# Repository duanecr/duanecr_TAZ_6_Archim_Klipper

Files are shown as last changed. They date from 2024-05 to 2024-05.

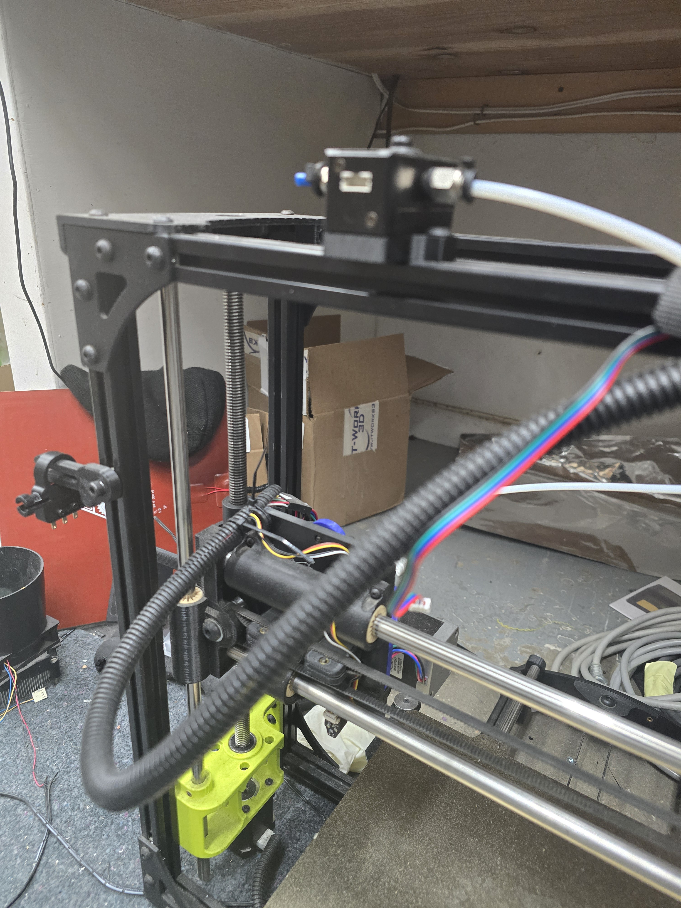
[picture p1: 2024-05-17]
TAZ6_Project/Manuals/SFS V2.0 Mount Location 2.jpg

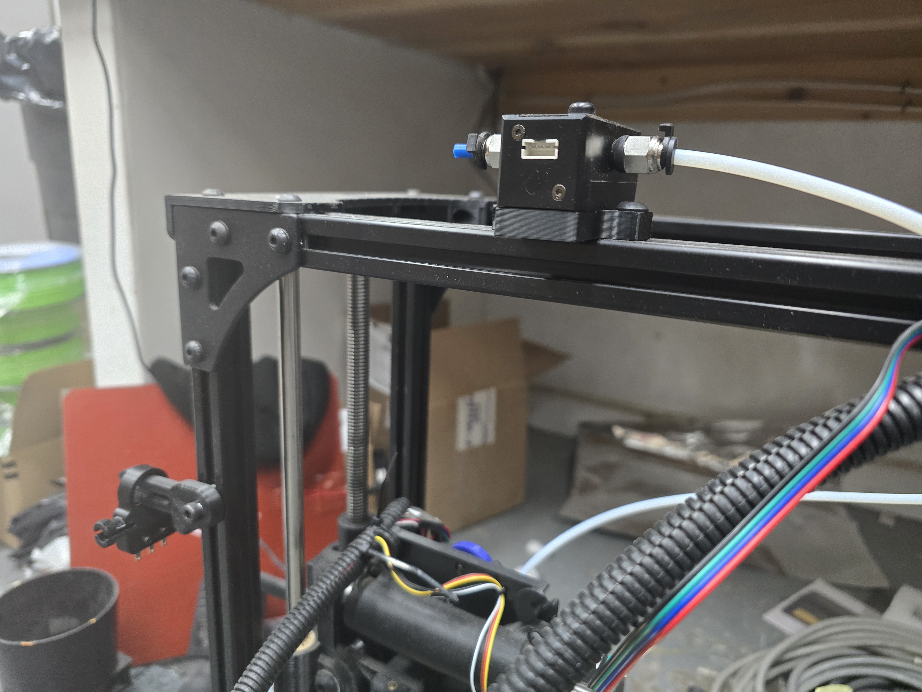
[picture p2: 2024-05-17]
TAZ6_Project/Manuals/SFS V2.0 Mount Location 1.jpg

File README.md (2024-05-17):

# duanecr_TAZ_6_Archim_Klipper
Configuration files for Lulzbot TAZ 6 using an Archim 2 board with a BTT PAD 7 for Klipper

Klipper Links

https://www.klipper3d.org/

https://github.com/Klipper3d/klipper

https://github.com/Klipper3d/klipper/tree/master/docs

Mainsail documentation
https://docs.mainsail.xyz/

**Initial Setup and Configuration**
• Install Klipper on a device if needed
○ Installation - Klipper documentation (klipper3d.org)
https://www.klipper3d.org/Installation.html
• Install Moonraker
	○ Installation - Moonraker
	https://moonraker.readthedocs.io/en/latest/installation/
• Install Klipperscreen for touchscreens
	○ Installation - KlipperScreen
	https://klipperscreen.readthedocs.io/en/latest/Installation/#auto-install
• Install Lulzbot version of Cura
	○ https://www.lulzbot.com/cura
• Verify printer bed is clean and empty
• Turn on printer
• Turn on device running Klipper
• Verify amount of filament on spool
• Verify thickness of filament for imperfections
• Connect web browser to http://taz.local and verify connectivity
• Open Cura and run through install steps for local printer
• Install Moonraker plugin for Cura
• Connect to Klipper
• Set the theme settings
	○ Lulzbot Lime Green
		§ rgb(194, 215, 53)
		○ Mainsail Quicktips | Themes
	https://youtu.be/kbSfLQtl4tA?si=HL7WomTxeTPDtKlo
	• Check E-Steps by running ??? command.
	• Use Orca calibration to check all of the settings
		○ Calibration · SoftFever/OrcaSlicer Wiki (github.com)
  		https://github.com/SoftFever/OrcaSlicer/wiki/Calibration

**Cura Print Settings**
Build plate adhesion type, determine whether to print on raft, skirt, or brim
Generate support or tree support
Infill density
Uncheck "keep heating" for build plate in Material section
Change "Z Seam Alignment" to shortest or random for round prints
 
**Initial Calibration Sites**
Teaching Tech 3D Printer Calibration (teachingtechyt.github.io)
https://teachingtechyt.github.io/calibration.html
Welcome! | Ellis’ Print Tuning Guide (ellis3dp.com)
https://ellis3dp.com/Print-Tuning-Guide/
 
New Printer Setup
Complete beginner's guide to 3D printing - Assembly, tour, slicing, levelling and first prints
https://youtu.be/T-Z3GmM20JM
 
Verify Extruder E-Steps
Run 100mm of filament through extruder to verify it is correct.  Adjust as needed.
[Teaching Tech 3D Printer Calibration (teachingtechyt.github.io)](https://teachingtechyt.github.io/calibration.html#esteps)

Set PID Autotune
[G-Codes - Klipper documentation (klipper3d.org)](https://www.klipper3d.org/G-Codes.html#pid_calibrate_1)
https://www.klipper3d.org/Config_checks.html?h=pid_calibrate#calibrate-pid-settings
PID_CALIBRATE HEATER=<config_name> TARGET=<temperature> [WRITE_FILE=1]
PID_CALIBRATE HEATER=heater_bed TARGET=60
PID_CALIBRATE HEATER=extruder TARGET=205

SAVE_CONFIG

Set Z Offset
Check Z-Offset
[Probe calibration - Klipper documentation (klipper3d.org)](https://www.klipper3d.org/Probe_Calibrate.html?h=z+offset#calibrating-probe-z-offset)
PROBE_CALIBRATE
SAVE_CONFIG
PROBE_ACCURACY

Resonance Compensation
https://www.klipper3d.org/Resonance_Compensation.html

Pressure Advance
https://www.klipper3d.org/Pressure_Advance.html

Bed Mesh Calibration
https://www.klipper3d.org/G-Codes.html#bed_mesh_calibrate
 
Calibration Source Information
https://teachingtechyt.github.io/calibration.html
Retraction calibration code site - http://prahjister.duckdns.org

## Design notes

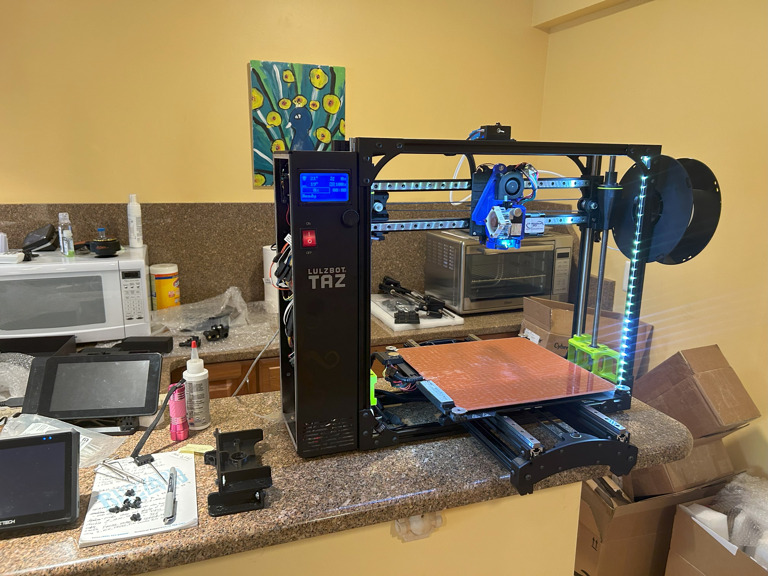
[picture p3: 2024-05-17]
TAZ6_Project/Pictures/20240410_190605491_iOS.jpg

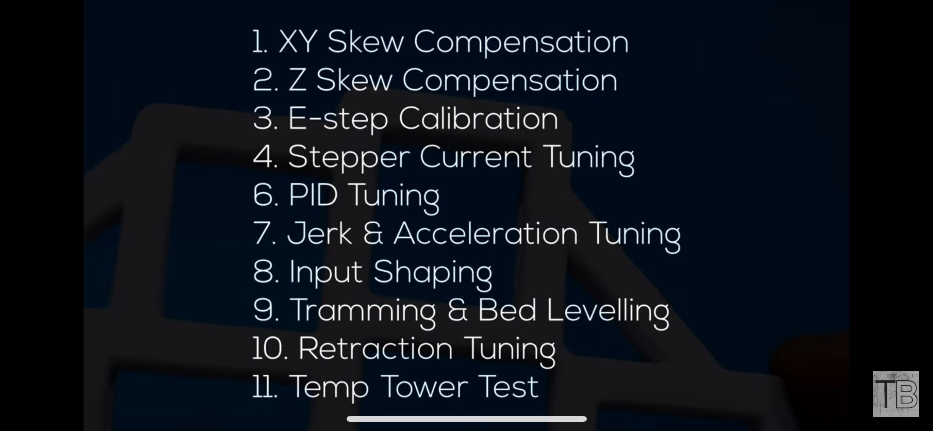
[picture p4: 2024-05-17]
TAZ6_Project/Pictures/20240403_203024000_iOS.png

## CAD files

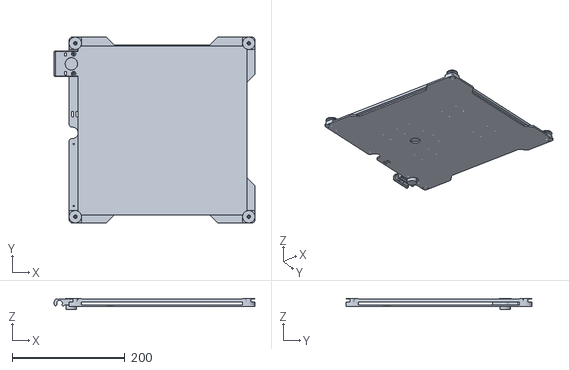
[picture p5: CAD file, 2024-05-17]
TAZ6_Project/Lulzbot TAZ 6 Build Plate.stl
356.9 x 330.0 x 20.2

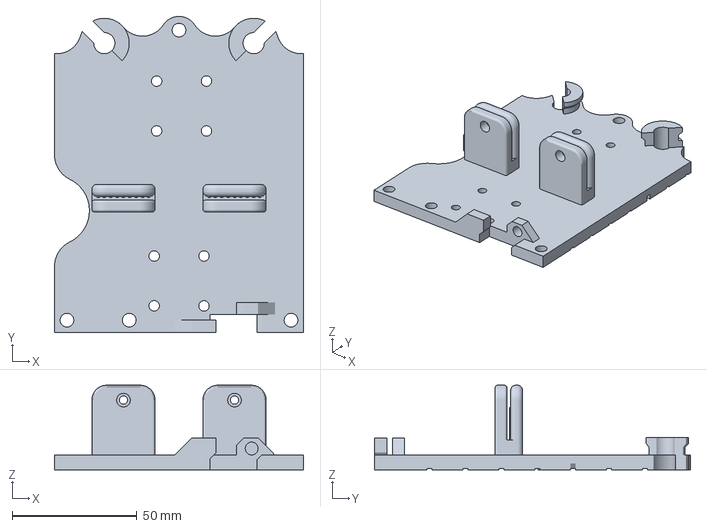
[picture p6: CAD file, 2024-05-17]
TAZ6_Project/Manuals/3D Models/TAZ 6 X Carriage Biqu MicroProbe Mount_LinearRail.3mf
100.0 x 127.0 x 34.0 mm

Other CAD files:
TAZ6_Project/Lulzbot TAZ 6 Build Plate.f3d

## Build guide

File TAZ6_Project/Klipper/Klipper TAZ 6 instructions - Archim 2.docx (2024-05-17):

Klipper/Touch Screen instructions for TAZ 6

These steps will get you setup with basic Klipper and MainSail to operate your TAZ 3D Printer. We would recommend familiarizing yourself with Klipper Language a bit via web search/YouTube videos. This will help your installation

First thing we recommend is to remove the SD card from the Pad7 and back-up all the files onto your computer somewhere just in case anything happens to it.

First things we will be doing is installing the new X Carriage. We have provided an ABS X Carriage that you will install onto your carriage mounts that has a built in spot for the Biqu MicroTouch ABL sensor. There are 2 screws/serts that you will use to install the probe onto the X carriage before installing it onto your printer. Remove your existing X carriage. Once the probe is installed correctly, install the Entire x carriage onto your printer. You can run a new belt at this point if you have one. You will re-use your current lower toolhead mount on the bottom of the X carriage. There are zip tie locations built into the X Carriage to route your wiring up the backside of the carriage for the MicroProbe.

You will need to run the wiring from the MicroProbe to the back of the machine where the wiring goes into the control box. You can run it in the same wiring that the toolhead wiring goes through. You will need to remove the small interconnect cover that houses the connections from the external wiring to the internal wiring (six screws). We have supplied a lengthened wiring harness that will connect the MicroProbe to the Rambo. See the Diagram below to see where the connectors will plug in. You will need to remove the wiring for the Z min endstop. The White and Black wires will plug into the Z-Min end-stop location, white wire to the left side. The Red/Brown will plug into the Serial connector location to the far right just to the left of the single 5 amp fuse. The brown wire will go into the top right pin. Yellow will go into pin 20 in the SPIO connector

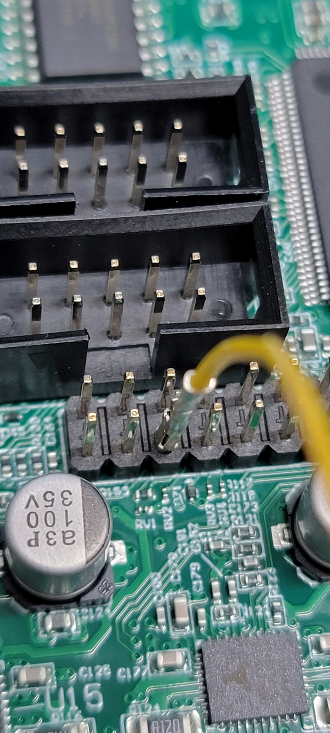
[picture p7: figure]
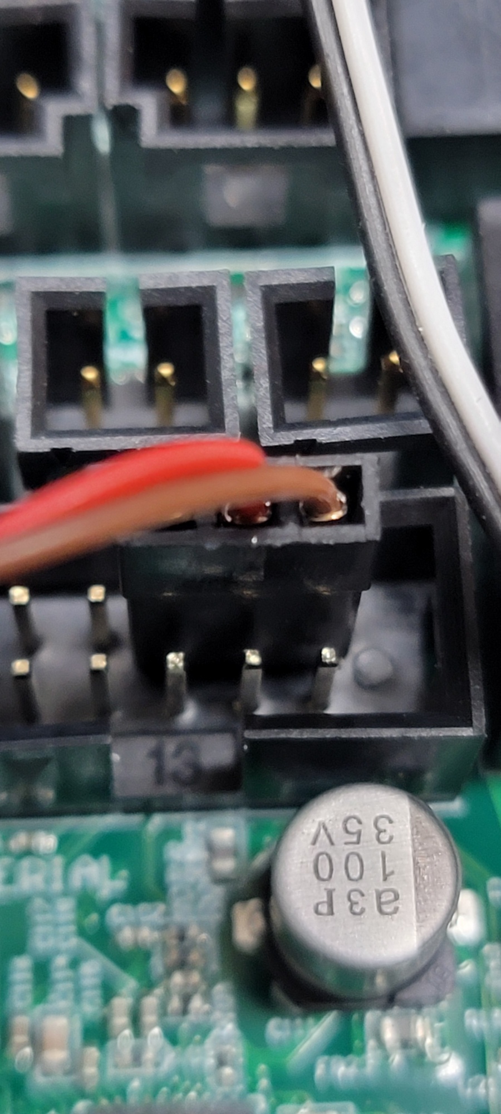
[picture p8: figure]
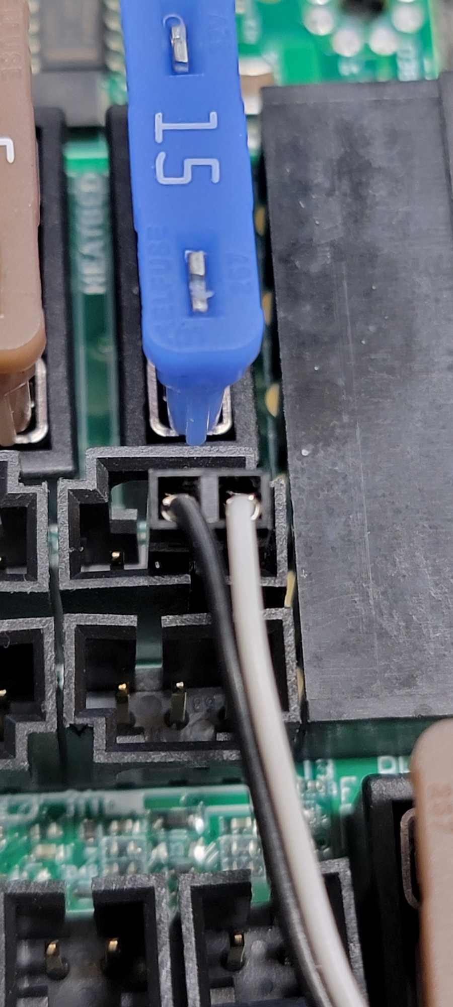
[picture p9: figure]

Button up all the wiring in the control box, and reinstall the interconnect cover. You can either add a new small section of wiring loom, or install it in to the current loom (it’s a bit tight already). If you add a new loom for the probe, just zip tie it to the existing toolhead harness all the way down to your toolhead. Re-install your toolhead and toolhead connector.

You will need to remove your BTT Pad 7 from the box and find a suitable location for it next to your printer. It will require a power box to be plugged in so make sure you have enough plug-ins available at your printer location. When turning it on, you will want to go ahead and set your Wi-Fi up with your SSID and password. Once you set it setup. Go ahead and restart the touchpad, and bring up your Wi-Fi menu once again and it should show you the IP Address that has been designated.

You will need to download a program called Putty so that you can SSH into your Pad7. If you search for Putty Download, you should see it come up. Get it setup on your computer you will be using to talk to your Pad7. Open the Putty program and you will see a window with Host Name. Enter in btt-pad7 and the SSH button below should be checked. Click Open at the bottom of the window. A new screen will open up and ask you for a user and password. Both user and password are biqu/biqu. From there you will be logged into the pad7. Complete the following steps to build and flash the Klipper Firmware to your printer Main Board (Rambo). Be sure you have a USB cable attached from y our Pad7 to the TAZ printer. It will need to be connected from here on out.

Type cd ~/klipper/

Type make menuconfig

Configure your settings according to the micro controller you are using.

Stock Rambo board (Taz6, Mini1, Mini2)

AVR atmega2560

Archim2 board (Taz6)

SAM3x8e

Type make

Plug in the printer via USB to pi and power it on.

Type ls /dev/serial/by-id/*

You printer should appear and look something like this. This is a unique ID and you'll need it later for the config file as well.

/dev/serial/by-id/usb-1a86_USB2.0-Serial-if00-port0

Now it's time to flash your board. Replace the ID with the one you got in the previous step.

Type sudo service klipper stop

Type make flash FLASH_DEVICE=/dev/serial/by-id/usb-1a86_USB2.0-Serial-if00-port0(this ID is just used for example, use the one provided in earlier steps)

Type sudo service klipper start

Reboot everything type sudo reboot

You will need to use the ID that you got from these steps in your printer.cfg file that we provide so it can talk to your printer. You will copy and paste that into the printer.cfg file a bit later on. You can go ahead and close out of your Putty Config window.

You can now use the IP address that your Pad7 got earlier on in the Wi-Fi steps. Type it into your browser with your Pad7 turned on. You will see an error message for now, but please disregard this for the time being. Once you are logged into the PAD7 from your browser you will see a set of icons on the left side of your screen. Click the machine icon, and this will open up a window that will show your configuration files associated with the PAD7 and klipper. You will need to upload the files for this part of the install; printer.cfg, that has been provided to you. Once the printer.cfg uploaded, open the printer.cfg file and up top you will need to paste your /dev/serial/by-id/* up top in the printer.cfg file so it can communicate with the board. You will need to go back to your Dashboard and then restart your firmware so it can communicate with the new build. The error that was on your screen should now be gone, and you should have a screen that shows homing, temperatures, etc.

The printer.cfg file is where the toolhead/stepper motor/printer info is stored. We have supplied you with files that you will need to rename to printer.cfg for them to work properly. You will need to be sure in the printer.cfg file, your toolhead does NOT have hash tags in front of each line. There should be a section for the stock toolhead, and a section for a Titan Aero toolhead. There you can set your filament diameter as well.

At this point make sure you X Axis is level across the bed meaning that you could run your nozzle across manually and it would be the same from the left side of the bed to the right. Turn your threaded rods until you can run it across and have it be the same on both sides. You can then click the Home button for each axis to ensure everything is working and moving as it should. X axis should home to the left side, the Y axis should home to the Back, and Z should go to the middle of the bed, and probe that location for Z. When you are homing each axis, be close to your printer on/off switch in case anything goes wrong.

Heat your bed up to at least 60C or whatever filament temp you are normally printing with. From your browser or the Pad7, you should be able to go into your height map menu or the config menu on the pad7 and go into bed mesh, and start the calibration. This will show you what your bed looks like and create a map for it to get the best first layer. In some cases you may need to shim your bed corners depending on what your first layer looks like if it can either compensate for it, or not. That will all depend on your bed. Again, be sure your X axis is level with the bed. It will give you the best possible starting point.

If you have specific Estep numbers saved from before, this is when you will change them. You can find a Estep to rotation distance convertor by searching online. Once you get that number you can replace it with the current rotation distance. You can check by telling the printer to extrude 100mm of filament and physically marking your filament at 100mm to ensure it send 100mm through it from the top at printing temperature.

We have the printer.cfg file setup to print a purge line at the front of the bed before it makes it over to your print. If you want this turned off, you can find the purge line in the cfg file, and put a hash in front of it to comment it out and not do the purge line.

How to install the 1.75mm Filament Runout/Motion Sensor

You will start by mounting your filament runout sensor in whichever configuration you want to run your filament with. We have provided a bracket for both top side configuration and a Top only configuration. See pics below for how we mounted our 1.75mm runout sensor. If you want to create your own bracket, reach out to us we can provide you with a STEP file to create your own based on your needs.

We have pinned your filament runout sensor so all you have to do is put the wires to their correct locations. Looking at the 24 pin SPIO connector, the Red will go into pin 24, black on pin 23 Blue on Pin 16 and green will do to Pin 15. SEE PICS FOR LOCATIONS.

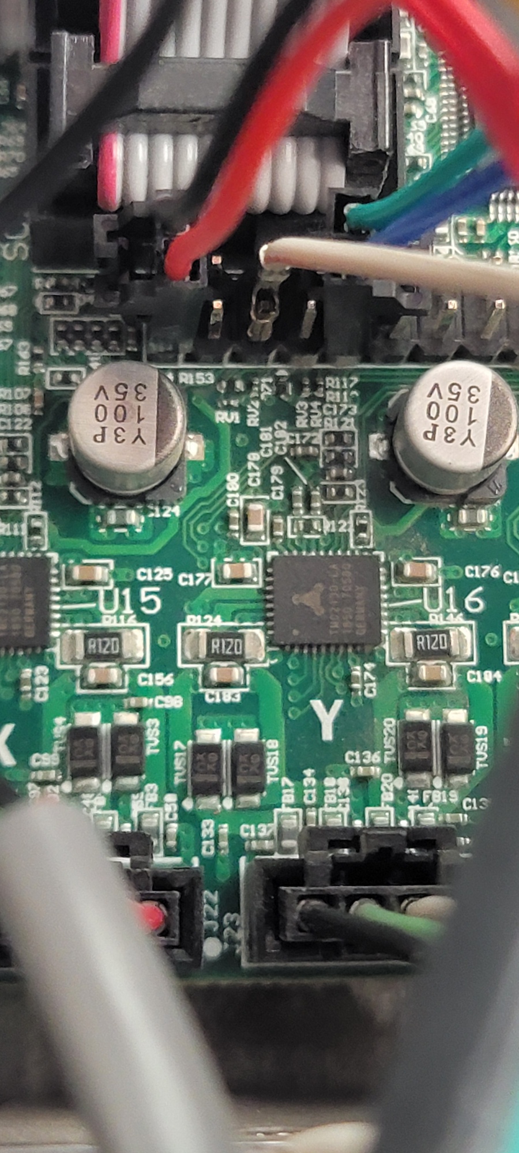
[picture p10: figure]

Keep in mind, the filament run-out/motion sensor will only work with 1.75mm filament. Now would be a great time to upgrade to a 1.75mm toolhead if you don’t already have one. We offer a wide range of 1.75mm toolheads. Toolhead that flow more and can keep up with higher speeds can be beneficial here. CHT nozzles as well as things like REVO HF can help out with that as well.

How to install the 2.85mm Filament Runout Switch

The 2.85/3mm sensor will install into some of the same pins as the 1.75mm, so if you are using the 2.85mm just swap the connectors for the pins shown in the photos below. You will be using the SPIO connector for this and the red will go into the 2nd pin to the right from the yellow wire from the MicroProbe, and the black will go into the Serial Connector lower left pin. Bottom left pin which is a ground. The red wire in this setup goes in the same location as the blue wire in the 1.75mm sensor. See pic above for location image.

HOW TO SETUP AND USE THE ADXL345 FOR INPUT SHAPER

We have already added the file necessary to use the ADXL345 provided with the PAD7. We have also added the necessary config tags into the printer.cfg file and adxl.cfg file that is necessary to work.

Start with the units power off, plug the adxl345 harness into the sensor itself, and then into the Pad7. To run input shaper on the y axis you will need to remove your wiper pad from the Y axis. You can use one of the screws to mount your adxl sensor to the bed plate. Make sure your wiring can move to the and have it not overextend or get caught anywhere. You will need to go into your printer.cfg file and remove the # from [include adxl.cfg]. Go into your console and run the following command: accelerometer_query. You should get a reading if working as it should. Home all axis, then you will type in shaper_calibrate axis=y. It will run a series of resonance tests. Once it’s finished up, it will show you the results, and ask you to save config. Go ahead and save, then restart Klipper and let it come back up to the dashboard. Go back into your printer.cfg file, and then scroll down to the very bottom. You should see those results posted there. Now you will be the same for your X axis. Attach the adxl to your toolhead somewhere, we mounted ours to one screw on the fan. Run the test again, and save like before. Save config and go back into your printer.cfg file and scroll to the bottom again and see if it saved those settings. If so you are done with input shaping. Keep in mind you will be required to do any tuning to your printer. We will not provide profiles for anything. Input shaping can only help so much so be sure to perform any calibration prints as necessary to get the best possible prints.

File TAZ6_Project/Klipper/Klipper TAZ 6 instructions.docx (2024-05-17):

Klipper/Touch Screen instructions for TAZ 6

These steps will get you setup with basic Klipper and MainSail to operate your TAZ 3D Printer. We would recommend familiarizing yourself with Klipper Language a bit via web search/YouTube videos. This will help your installation

First thing we recommend is to remove the SD card from the Pad7 and back-up all the files onto your computer somewhere just in case anything happens to it.

First thing we will be doing is installing the new X Carriage. If you have a linear rail conversion and we sent you the X carriage for a stock setup, please let us know we can get you the correct X Carriage.

There are 2 screws/serts that you will use to install the probe onto the X carriage before installing it onto your printer. Remove your existing X carriage. Once the probe is installed correctly, install the Entire x carriage onto your printer. You can run a new belt at this point if you have one. You will re-use your current lower toolhead mount on the bottom of the X carriage. There are zip tie locations built into the X Carriage to route your wiring up the backside of the carriage for the MicroProbe.

You will need to run the wiring from the MicroProbe to the back of the machine where the wiring goes into the control box. You can run it in the same wiring that the toolhead wiring goes through. You will need to remove the small interconnect cover that houses the connections from the external wiring to the internal wiring (six screws). We have supplied a wiring harness that will connect the MicroProbe to the Rambo/Archim. See the Diagram below to see where the connectors will plug in. You will need to remove the wiring for the Z min endstop. The White and Black wires will plug into the Z-Min endstop location. The Red/Brown will plug into the Motor EXT1 MX3 location to the far right. Red pin will go in the #1 location and brown right next to it. The Yellow will plug into the MX1 position #3 which is the bottom of EXT1 in the very middle.

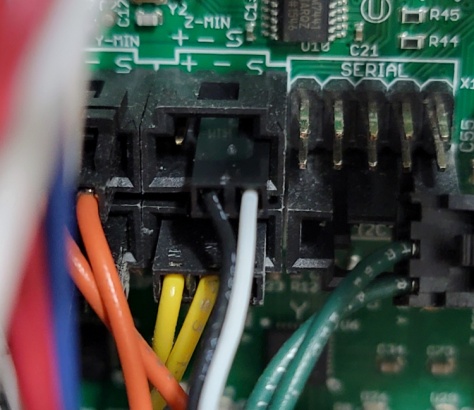
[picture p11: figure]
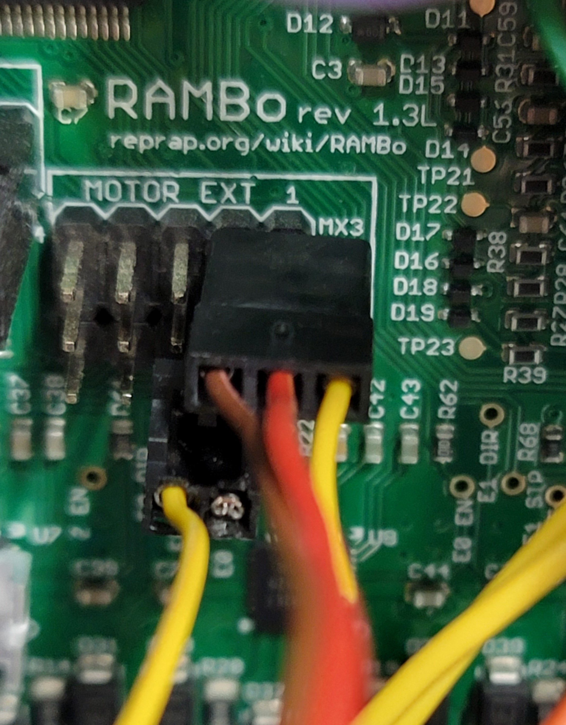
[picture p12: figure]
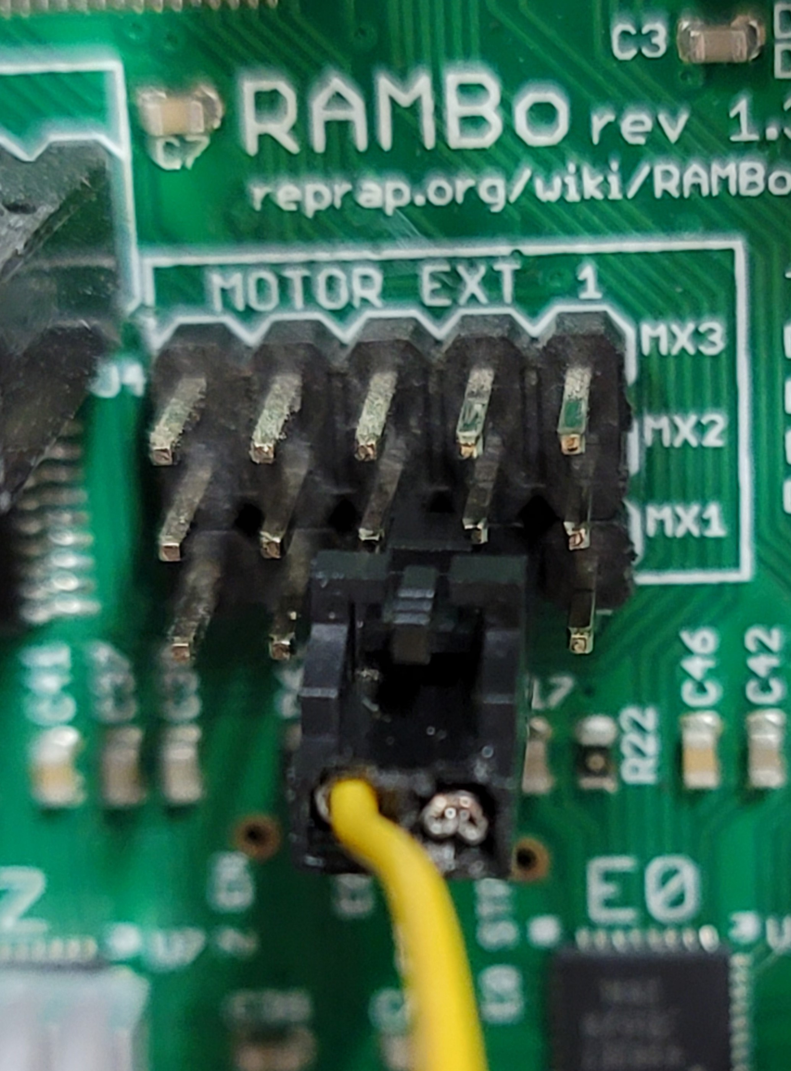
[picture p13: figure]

Button up all the wiring in the control box, and reinstall the interconnect cover. You can either add a new small section of wiring loom, or install it in to the current loom (it’s a bit tight already). If you add a new loom for the probe, just zip tie it to the existing toolhead harness all the way down to your toolhead. Re-install your toolhead and toolhead connector.

Next, you will need to remove your BTT Pad 7 from the box and find a suitable location for it next to your printer. It will require a power box to be plugged in so make sure you have enough plug-ins available at your printer location. When turning it on, you will want to go ahead and set your Wi-Fi up with your SSID and password. Once you set it setup. Go ahead and restart the touchpad, and bring up your Wi-Fi menu once again and it should show you the IP Address that has been designated.

You will need to download a program called Putty so that you can SSH into your Pad7. If you search for Putty Download, you should see it come up. Get it setup on your computer you will be using to talk to your Pad7. Open the Putty program and you will see a window with Host Name. Enter in btt-pad7 and the SSH button below should be checked. Click Open at the bottom of the window. A new screen will open up and ask you for a user and password. Both user and password are biqu/biqu. From there you will be logged into the pad7. Complete the following steps to build and flash the Klipper Firmware to your printer Main Board (Rambo). Be sure you have a USB cable attached from y our Pad7 to the TAZ printer. It will need to be connected from here on out.

Type cd ~/klipper/

Type make menuconfig

Configure your settings according to the micro controller you are using.

Stock Rambo board (Taz 5, 6)

AVR atmega2560

or

Archim2 board (Taz6)

SAM3x8e

Type make

Plug in the printer via USB to pi and power it on.

Type ls /dev/serial/by-id/*

You printer should appear and look something like this. This is a unique ID and you'll need it later for the config file as well.

/dev/serial/by-id/usb-1a86_USB2.0-Serial-if00-port0

Now it's time to flash your board. Replace the ID with the one you got in the previous step.

Type sudo service klipper stop

Type make flash FLASH_DEVICE=/dev/serial/by-id/usb-1a86_USB2.0-Serial-if00-port0(this ID is just used for example, use the one provided in earlier steps)

Type sudo service klipper start

Reboot everything type sudo reboot

You will need to use the ID that you got from these steps in your printer.cfg file that we provide so it can talk to your printer. You will copy and paste that into the printer.cfg file a bit later on. You can go ahead and close out of your Putty Config window.

You can now use the IP address that your Pad7 got earlier on in the Wi-Fi steps. Type it into your browser with your Pad7 turned on. You will see an error message for now, but please disregard this for the time being. Once you are logged into the PAD7 from your browser you will see a set of icons on the left side of your screen. Click the machine icon, and this will open up a window that will show your configuration files associated with the PAD7 and klipper. You will need to upload the files for this part of the install; printer.cfg, that has been provided to you. Once the printer.cfg uploaded, open the printer.cfg file and up top you will need to paste your /dev/serial/by-id/* up top in the printer.cfg file so it can communicate with the board. You will need to go back to your Dashboard and then restart your firmware so it can communicate with the new build. The error that was on your screen should now be gone, and you should have a screen that shows homing, temperatures, etc.

The printer.cfg file is where the toolhead/stepper motor/printer info is stored. We have supplied you with files that you will need to rename to printer.cfg for them to work properly. You will need to be sure in the printer.cfg file, your toolhead does NOT have hash tags in front of each line. There should be a section for the stock toolhead, and a section for a Titan Aero toolhead. There you can set your filament diameter as well.

For setting your toolhead esteps you will be changing the Rotation distance on the [extruder] portion of the cfg file. Again, you will also see there is a setup for either the stock toolhead or a Titan Aero toolhead. If you are going to use the Titan Aero you will need put a hash in from of the stock extruder settings or vice versa, and remove the hash from the extruder you wish to use.

At this point make sure you X Axis is level across the bed meaning that you could run your nozzle across manually and it would be the same from the left side of the bed to the right. Turn your threaded rods until you can run it across and have it be the same on both sides. You can then click the Home button for each axis to ensure everything is working and moving as it should. X axis should home to the left side, the Y axis should home to the Back, and Z should go to the middle of the bed, and probe that location for Z. When you are homing each axis, be close to your printer on/off switch in case anything goes wrong.

Heat your bed up to at least 60C or whatever filament temp you are normally printing with. From your browser or the Pad7, you should be able to go into your height map menu or the config menu on the pad7 and go into bed mesh, and start the calibration. This will show you what your bed looks like and create a map for it to get the best first layer. In some cases you may need to shim your bed corners depending on what your first layer looks like if it can either compensate for it, or not. That will all depend on your bed. Again, be sure your X axis is level with the bed. It will give you the best possible starting point.

If you have specific Estep numbers saved from before, this is when you will change them. You can find a Estep to rotation distance convertor by searching online. Once you get that number you can replace it with the current rotation distance. You can check by telling the printer to extrude 100mm of filament and physically marking your filament at 100mm to ensure it send 100mm through it from the top at printing temperature.

We have the printer.cfg file setup to print a purge line at the front of the bed before it makes it over to your print. If you want this turned off, you can find the purge line in the cfg file, and put a hash in front of it to comment it out and not do the purge line.

How to install the 1.75mm Filament Runout/Motion Sensor

You will start by mounting your filament runout sensor in whichever configuration you want to run your filament with. We have provided a bracket for both top side configuration and a Top only configuration. See pics below for how we mounted our 1.75mm runout sensor. If you want to create your own bracket, reach out to us we can provide you with a STEP file to create your own based on your needs.

We have pinned your filament runout sensor so all you have to do is put the connectors to their correct locations. Red will go into pin 1, black on pin 2 Blue on Pin 7 of the X40 Connector. Green will do to Pin 5 on the X34 connector. SEE PICS FOR LOCATIONS.

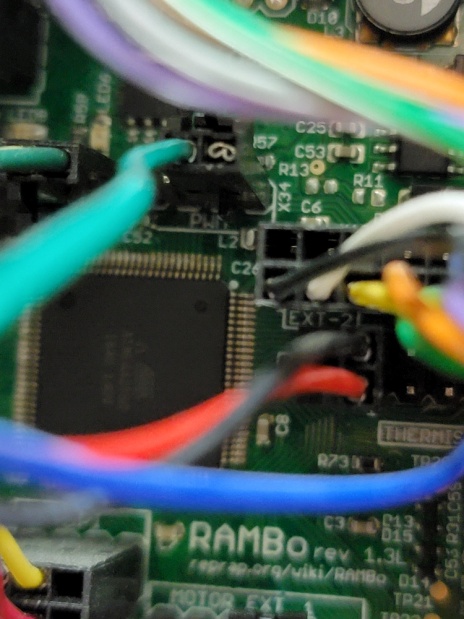
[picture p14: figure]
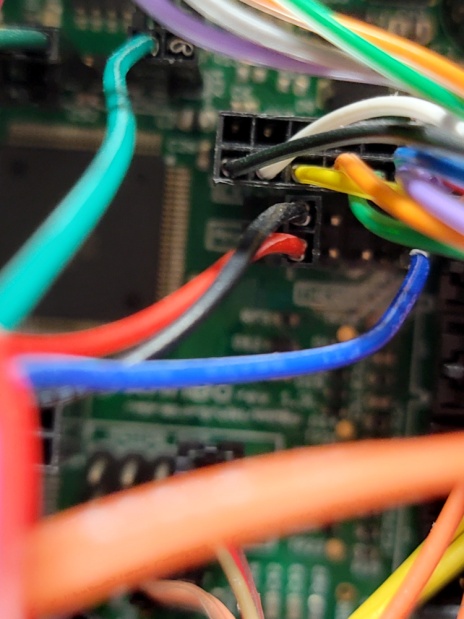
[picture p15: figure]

We have showed the connections with the Rambo 1.3L Main Board. These same instructions will work for the 1.4 as well, but one connector location is a bit different. You will need to locate the X34 and X 40 connectors. The X34 set is a 6 pin in line configuration just above the largest main chip on the board. The X 40 is over to the right side of the largest chip on the board.

Keep in mind, the filament run-out/motion sensor will only work with 1.75mm filament. Now would be a great time to upgrade to a 1.75mm toolhead if you don’t already have one. We offer a wide range of 1.75mm toolheads. Toolhead that flow more and can keep up with higher speeds can be beneficial here. CHT nozzles as well as things like REVO HF can help out with that as well.

How to install the 2.85mm Filament Runout Switch

The 2.85/3mm sensor will install into some of the same pins as the 1.75mm, so if you are using the 2.85mm just swap the connectors for the pins shown in the photos below. You will be using Pin 2 for the black wire, and pin 7 for the red wire of the X40 Connector.

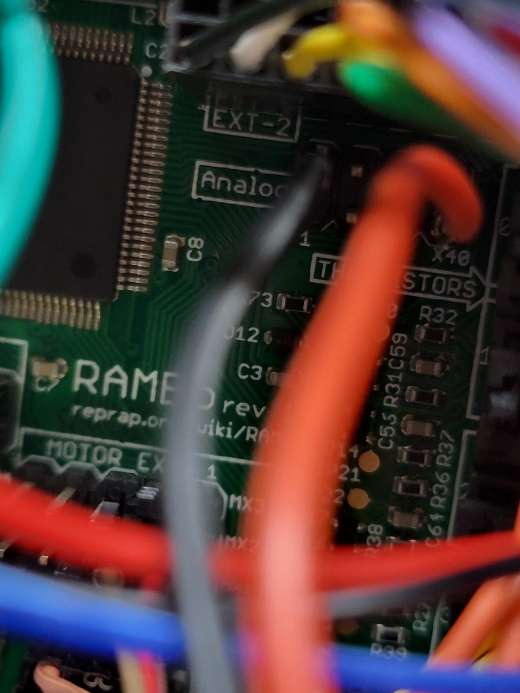
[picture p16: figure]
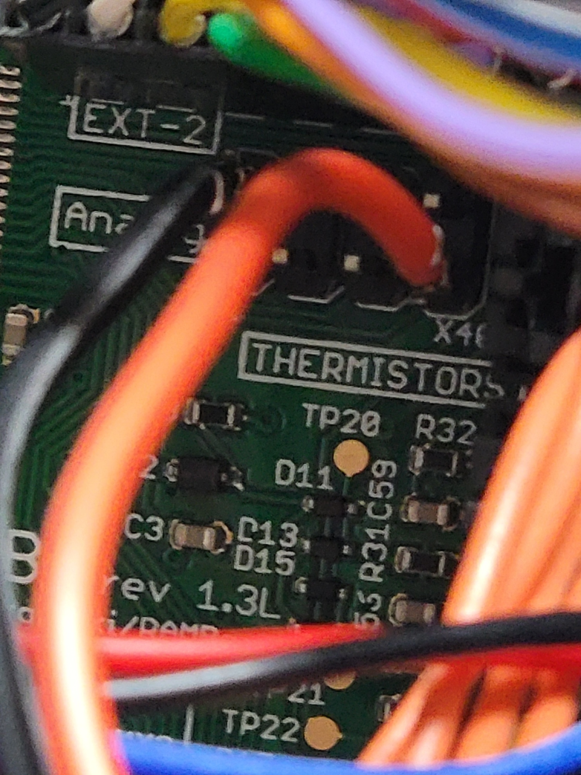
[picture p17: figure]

HOW TO SETUP AND USE THE ADXL345 FOR INPUT SHAPER

We have already added the file necessary to use the ADXL345 provided with the PAD7. We have also added the necessary config tags into the printer.cfg file and adxl.cfg file that is necessary to work.

Start with the units power off, plug the adxl345 harness into the sensor itself, and then into the Pad7. To run input shaper on the y axis you will need to remove your wiper pad from the Y axis. You can use one of the screws to mount your adxl sensor to the bed plate. Make sure your wiring can move to the and have it not overextend or get caught anywhere. You will need to go into your printer.cfg file and remove the # from [include adxl.cfg]. Go into your console and run the following command: accelerometer_query. You should get a reading if working as it should. Home all axis, then you will type in shaper_calibrate axis=y. It will run a series of resonance tests. Once it’s finished up, it will show you the results, and ask you to save config. Go ahead and save, then restart Klipper and let it come back up to the dashboard. Go back into your printer.cfg file, and then scroll down to the very bottom. You should see those results posted there. Now you will be the same for your X axis. Attach the adxl to your toolhead somewhere, we mounted ours to one screw on the fan. Run the test again, and save like before. Save config and go back into your printer.cfg file and scroll to the bottom again and see if it saved those settings. If so you are done with input shaping. Keep in mind you will be required to do any tuning to your printer. We will not provide profiles for anything. Input shaping can only help so much so be sure to perform any calibration prints as necessary to get the best possible prints.

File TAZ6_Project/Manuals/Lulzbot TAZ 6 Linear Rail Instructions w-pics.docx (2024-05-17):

Lulzbot TAZ 5/6 Y Axis Linear Rail
Conversion Instructions

IF DURING ANY POINT OF INSTALLATION YOU HAVE QUESTIONS, CALL OR EMAIL US BEFORE MOVING TO NEXT STEP.

First. Unplug the printer. Then, remove the 4 thumbscrews that hold your bed down to the printer. Then unplug the Y axis motor, Bed heater, thermistor and switch wiring. Remove the entire bed assembly from the printer and place in an easy to work in space.

Remove the 4 bed washers, screws and spacers from the bed assembly. Remove the build plate and set it aside somewhere safe. Turn the bed assembly upside down so you can see the bushing holders. Remove the 4 M3x8 button head screws that hold down each bushing holder and save the screws and washers as you will use these screws to mount the drill jig to the aluminum plate (shown in the images). Remove the 4 M3x8 button head screws and washers that hold down the Belt Mount. Remove the 4 M3x8 button head screws and washers that hold the Y End Idler on the front Y End Plate. Remove the 4 M3x8 button head screws and washers that hold on the Y End Motor Mount to the rear Y End Plate.

Mount the supplied 3D printed drill jigs to the aluminum bed plate with the M3x8 button head screws and washers you removed in the previous step.

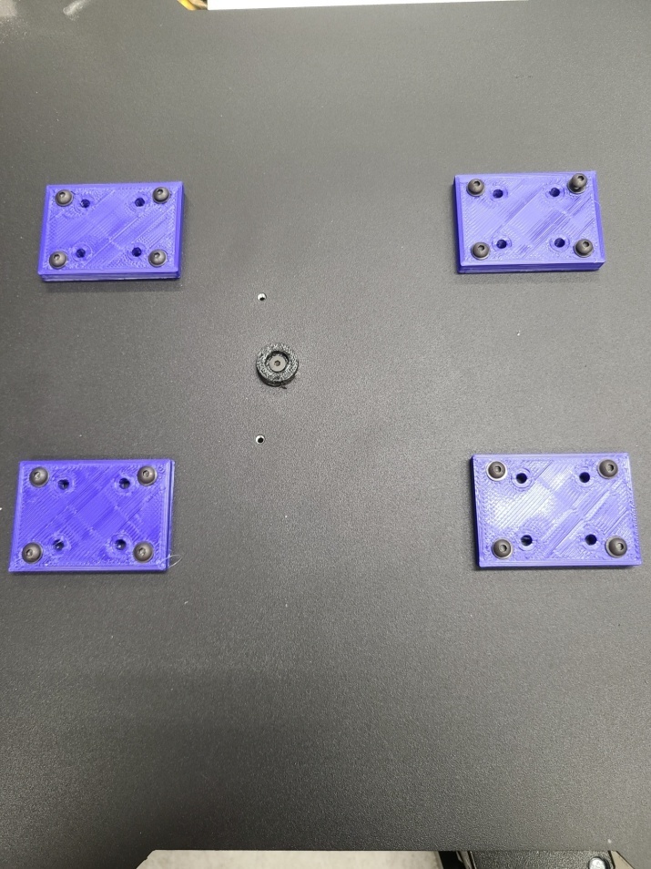
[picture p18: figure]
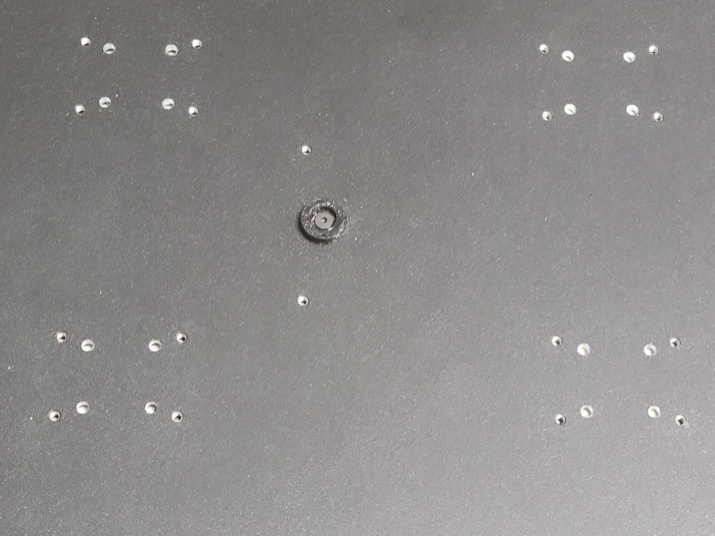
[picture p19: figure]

Place the aluminum bed plate on something flat like a piece of plywood. This will ensure you do not bend the aluminum plate. Drill each hole out with the supplied 9/16” drill bit. Now remove the drill jigs and deburr each hole drilled with a larger drill bit by hand spinning the bit just over each hole You want the hole free of anything sticking off of it so the linear rail carriage mounts flush.

Loosen the set screws that hold the smooth rods onto the 3d printer corners and remove them from the assembly. You can put the bushing holders back onto the rods and set them aside for storage. Remove the M5x10 button head screws and washers from the Y end plates from the bed assembly being sure to keep all hardware. Remove the M5x10 button head screws and washers holding the 3d printer corners/bed feet again keeping the hardware as it will go back in its original position. Set your 20x20 Extrusions aside for later use.

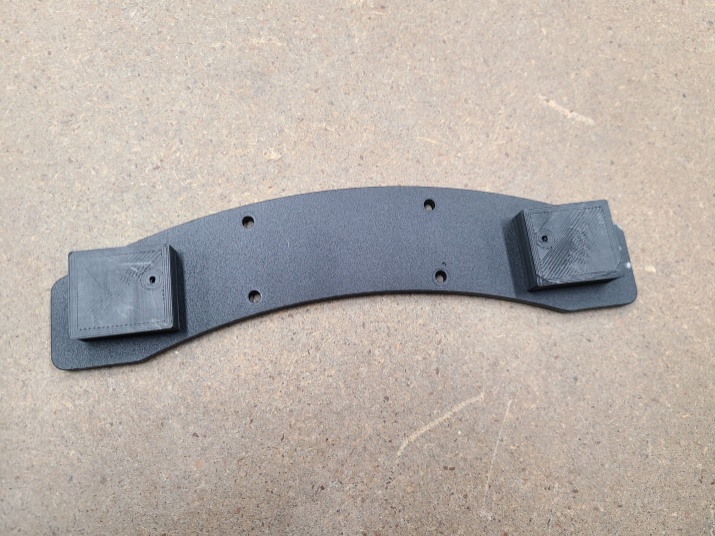
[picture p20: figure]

Now, you will need to drill out the Y End Plates to accept the 4 new additional M3x8 button head screws. IMPORTANT: Refer to the photo included to ensure correct positioning of the drill jig. Using the supplied drill jig and same drill bit used before, drill out one hole on each side of both the front and rear Y End Plates. Deburr the holes as necessary.

Remove the rubber feet from your old Bed Corners, and move them to the new Bed Corners. Take your original 20x20 Extrusions and put them into the 4 3d printed corners.

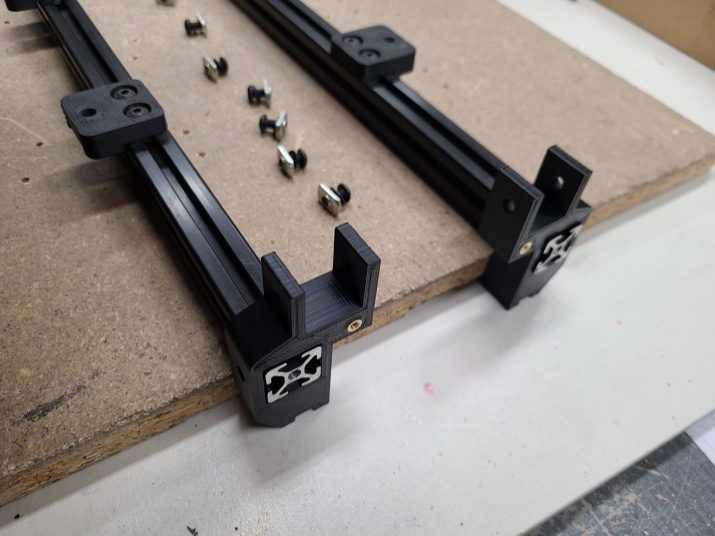
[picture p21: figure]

To ensure correct positioning, please refer to the photo.

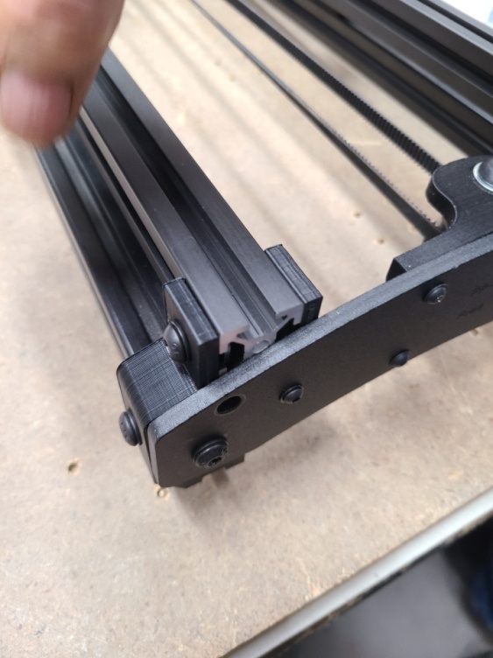
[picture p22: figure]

Make sure all your T- Nuts are in the original position. Locate the 20x20 Extrusions supplied in the kit and insert the 2 slide-in M5 T-Nuts supplied into each 20x20 Extrusions ends. Install both 20x20 Extrusions into the 3d printed corners. Refer to the photo for the correct location of the button head screws, washers and T-Nuts. Again, loosely fit the M5x10 button head screws and washers into the ends of the extrusions and through the Y End Plates. This will greatly aid in the rail alignment needed in a future step.

Install both Y End Plates with 4 M5x10 button head screw and washer onto the 3D printed corner but keep it loose for now. Also install the M3x8 button head screw and washer into the newly drilled hole, but keep it loose for now. Install the Y End Motor Mount and Y End Idler back onto the Y End plates using the M3x8 button head screws and washers you removed from them in earlier steps. NOTE: You may find it beneficial to route the belt over the motor gear during installation. Once in position, tighten only these screws.

Remove the linear rails from their packaging. You will need to clean the shipping residue from each rail. You can use isopropyl alcohol or any light solvent cleaner and a paper towel. Clean the bottom side of the carriages (where you see the ball bearings) as well. Be careful not to let the carriages fall off the rails or the ball bearings will fly out and will most likely never be found. Make sure the carriages move freely on the rails, as it will be harder to correct this later. You will lubricate these at the end of the installation.

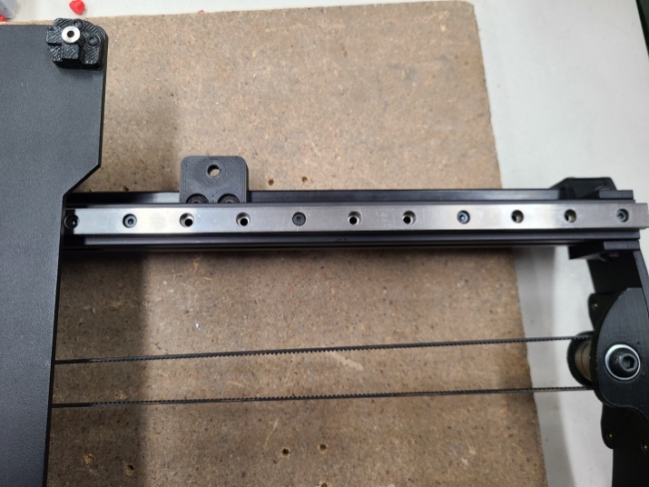
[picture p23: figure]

Place the Bed Rail Assembly right side up on the work surface. In the next step you will install 8 each M3x8 cap head screws and drop-in T-Nuts onto the linear rails. See photo.

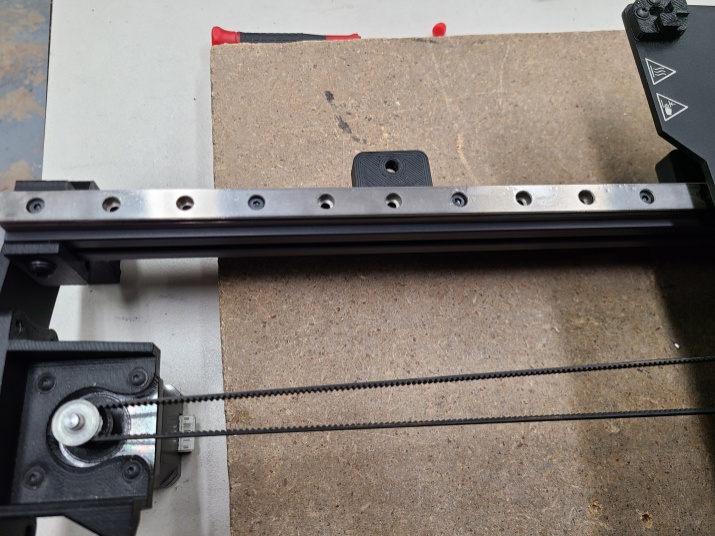
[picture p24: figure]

It helps if you 1st place the M3x8 cap head screw into the linear rail, and then attach the drop-in T-Nut to it. After you have attached all of your screws and t nuts, turn the t-nuts so they face with the opening of the rail so they will drop into the Extrusion. After all of these are in place, you can position the linear rails over the Extruder rails, drop them in, and loosely tighten them.

Take your Aluminum Bed Plate and place the Linear Rails Carriage side to the bottom of the Bed Plate and line up your holes to the holes you drilled in previous steps. Loosely install the 16 each M3x6 button head screws and washers. Do not fully tighten them. If they are too tight the linear rails will bind up, and right now they need to be loosely fit. They will need to be just tight enough to hold everything in place. You will have to play with this a bit to find the right tension in the final steps.

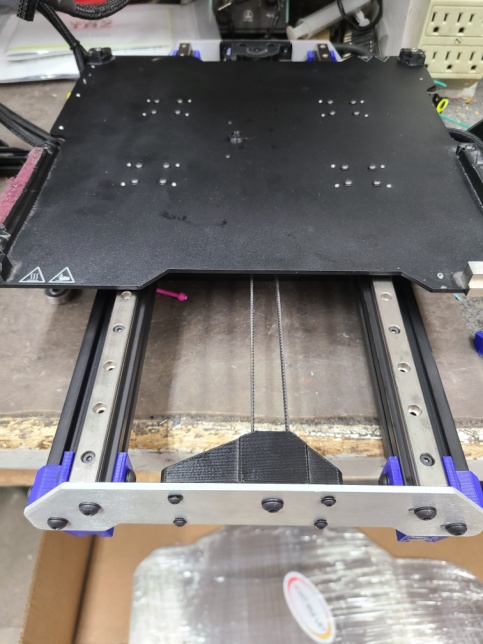
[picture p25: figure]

Loosely tighten the screws on the rail. When you start to tighten the screw, the t-nut will turn and grab the Extrusion. If you feel it doesn’t, unscrew your cap screw and try again until it grabs just a bit.

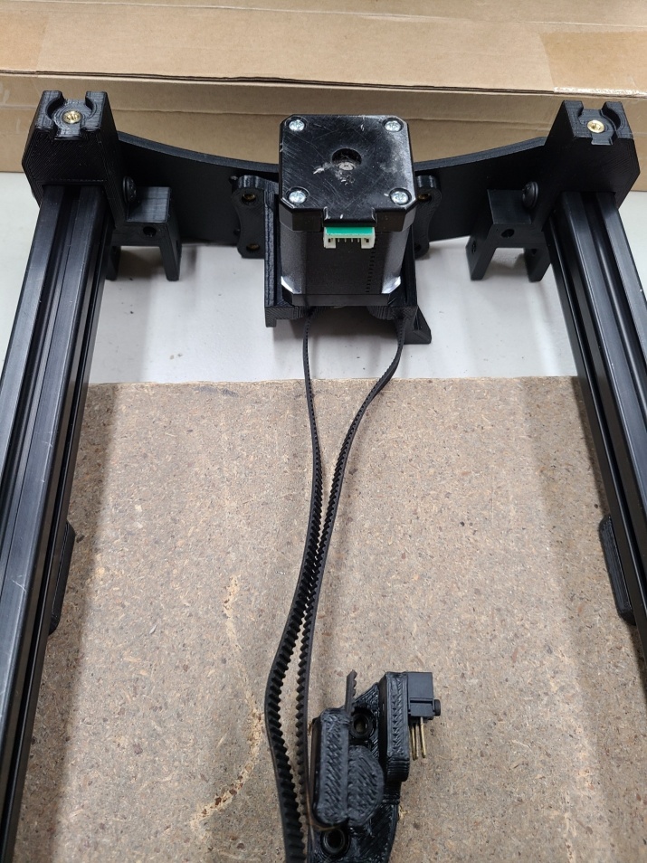
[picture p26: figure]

Now that you have your Bed Plate and Linear Rails attached to the Y axis you are almost done!! Reattach the belt tensioner mount to the Bed Plate using the 4 M3x8 button head screws and washers. Reattach the orange and blue wires to their corresponding switches. Re-attach the Y Axis to your printer and install the Y Axis thumbscrews. At this point, you will want to to tighten all screws down gently. Do not over tighten any of the screws, just make them snug. You will find that you may have to loosen and tighten things to get the rails to align to your liking. Once you have everything moving freely, you can install your Heated Bed back onto the Bed Plate and plug in the Y Axis Motor. Be sure you don’t try to move the bed back and forth manually with speed or you may back feed electricity into your LED Board and cause damage. Turn on your printer and home the axis to make sure everything moves as it should.

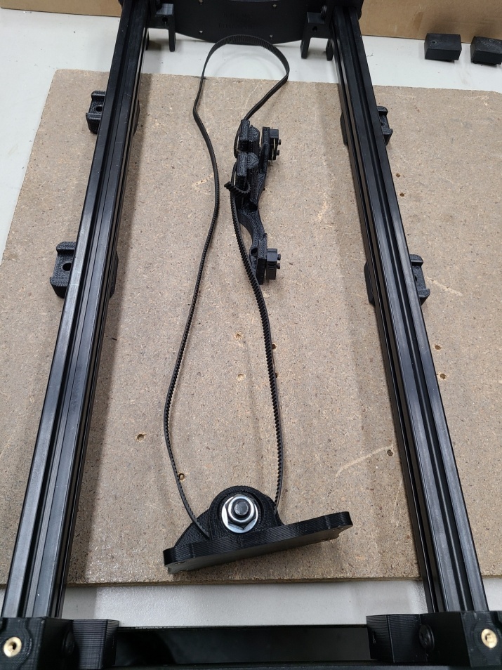
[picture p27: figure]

You will want to treat your Linear Rails with a low viscosity lubricant. Do not use graphite. Tri-Flow lubricant works well and doesn’t attract dust. It is a bit pricey but works well. You can use any silicone based lubricant as long as it doesn’t attract too much unwanted dust or debris.

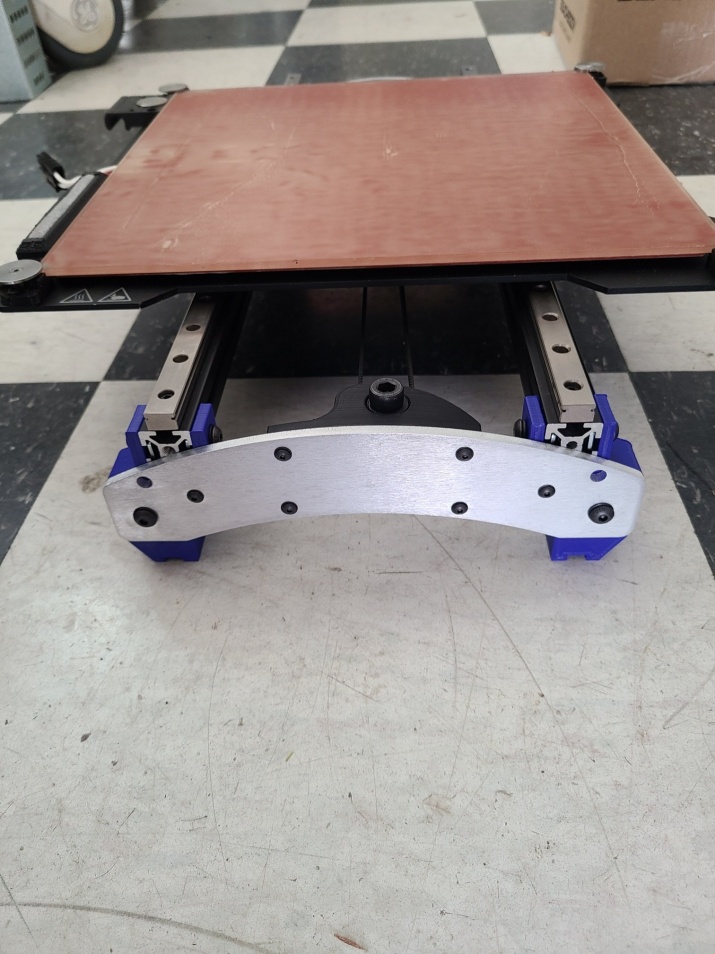
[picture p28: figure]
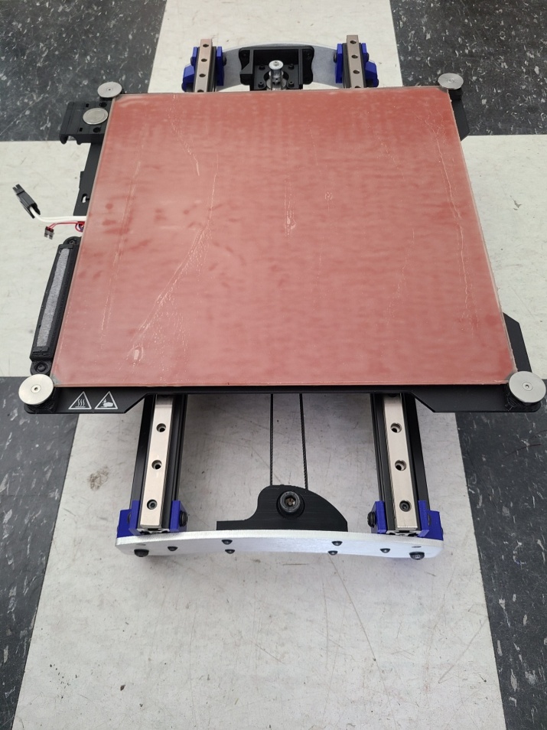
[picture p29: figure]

You are now finished with your Linear Rail Conversion!!!

If you have any questions, please email us at info@itworks3d.com.

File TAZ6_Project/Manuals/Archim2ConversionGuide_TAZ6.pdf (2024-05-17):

# Archim2 Conversion Guide

For the Lulzbot TAZ 6

v1.3
3/31/2020

## Contents

Included in the root directory is a spreadsheet that outlines the parts used, the STL model of the printed heatsink mount (both stock (http://download.lulzbot.com/TAZ/TAZ_Pro/v1.0.7/production_parts/printed_parts/heatsink_mount/) and modified as described in the Mechanical Section), and the design drawing for the heatsink from Lulzbot. (http://download.lulzbot.com/TAZ/TAZ_Pro/v1.0.7/production_parts/machined_parts/board_heatsink/Archim_board_heatsink.pdf) This information, as well as a wiring diagram are in the Appendix.

Disclaimer: You do this work at your own risk. Your warranty will likely be voided by doing this. It is up to the implementer if the advantages of doing this work outweigh the risks. Wiring, crimping, and soldering is involved.

# Purpose

The purpose of the guide is to assist users with a Lulzbot TAZ6 3d Printer in the conversion steps from the stock 8-bit, 16MHz RAMBo board to the 32-bit, 84MHz Archim2 board that is used in the Lulzbot TAZ Pro. Provided are the steps that I took to complete my conversion.

Why would you want to do this? There are a few primary reasons to do this conversion. First, the Archim2 uses a much faster microprocessor that has many more resources and native USB support. This allows for GCODE to be parsed and executed faster resulting in smoother movement during complicated geometries that require many lines to be processed and executed quickly (like circles that are made up of a great deal of line segments). The Archim2 also utilizes Trinamic TMC2130 stepper motor controllers which have several improvements and advantages over the Allegro A4982 motor controllers used on the RAMBo boards, including silent operation. Seriously, unless you are watching the printer, you can’t hear it! Also, with alternate firmware like Klipper can take advantage of the native USB to send instructions very fast.

PLEASE READ THIS ENTIRE DOCUMENT BEFORE ATTEMPTING THIS TO ENSURE THAT YOU HAVE PURCHASED AND/OR PRINTED EVERYTHING YOU WILL NEED!

# Where to Buy an Archim2 Board?

The Archim2 is made by UltiMachine and can be purchased from their site here: https://ultimachine.com/products/archim2?variant=13739792466029

Since this board will be replacing the RAMBo, one only needs to buy the “Assembled Circuit Board ONLY” (select under Kit Options). The NOTE on the bottom of the product page states:

“NOTE: If purchasing this board as a replacement for one received in another distributor's printer kit, please "Add a note to your order" ("notes" located in shopping cart view) prior to checkout regarding your printer's name/version/distributor details. The controller may require some adjustments for printer compatibility. Thank you!”

So, I went ahead and told them that this board was going into a Lulzbot TAZ6 and had no issues with the configuration I was sent. Note that the images on the site show the Archim2 2.1a, however, they are shipping the 2.2b. I have no clue what the difference is as nothing they have online (including the wiki) mention the 2.2b. I assume it is a trivial change (probably BOM related).

# Electrical

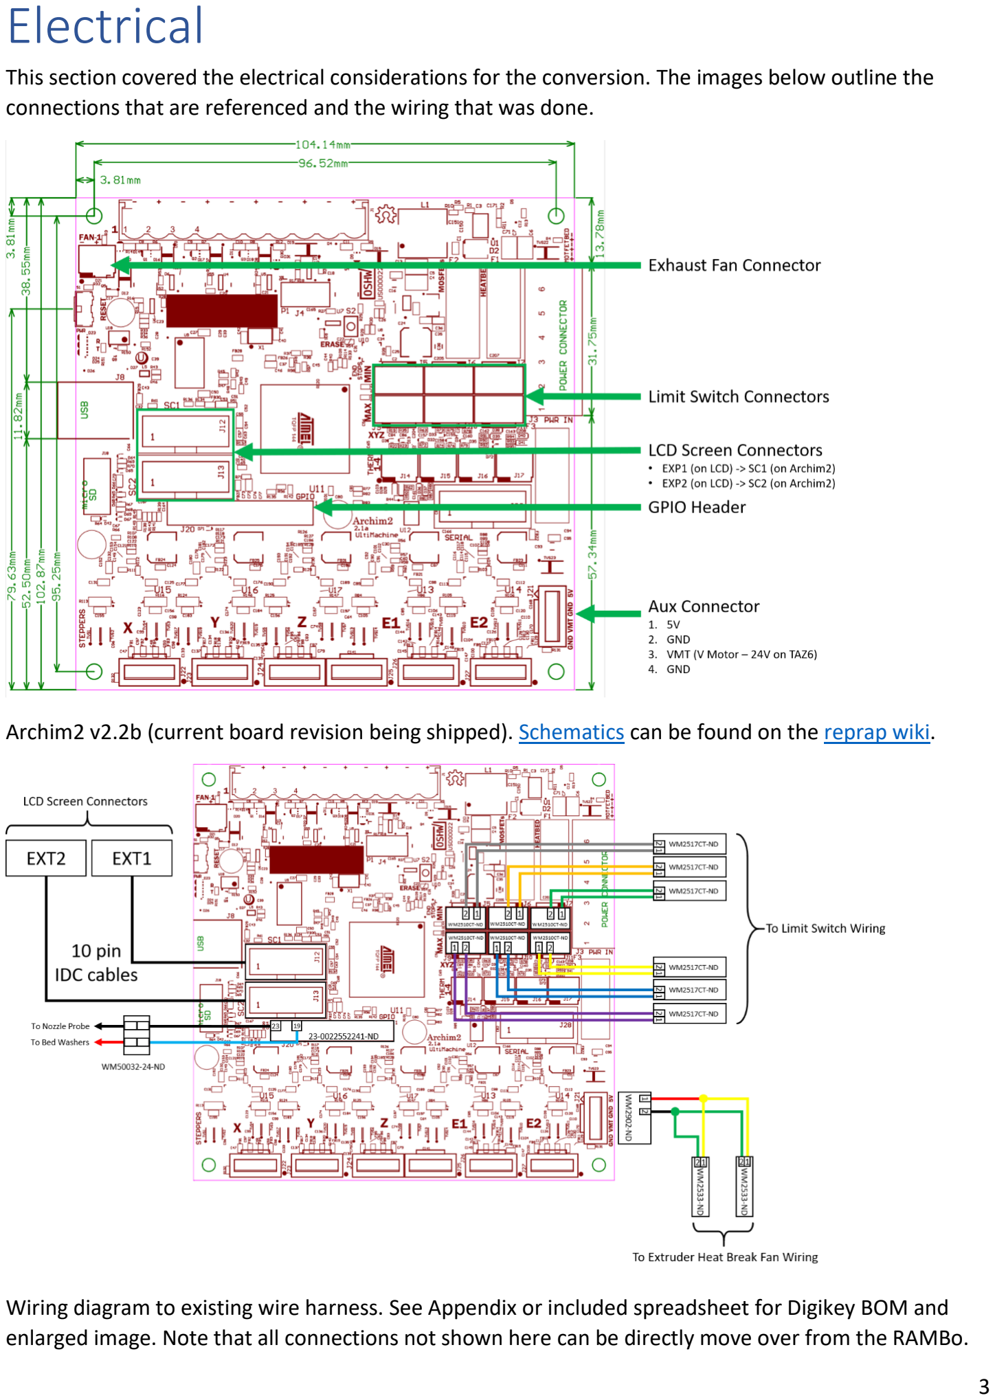
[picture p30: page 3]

This section covered the electrical considerations for the conversion. The images below outline the connections that are referenced and the wiring that was done.

Archim2 v2.2b (current board revision being shipped). Schematics (https://github.com/ultimachine/Archim/blob/c68ed12ccc4da3c50be3b65031d0f8b64b89efce/Project%20Outputs/Archim2_2.1a_Schematic.PDF) can be found on the reprap wiki. (https://reprap.org/wiki/Archim2)

Wiring diagram to existing wire harness. See Appendix or included spreadsheet for Digikey BOM and enlarged image. Note that all connections not shown here can be directly move over from the RAMBo.

# Limit Switch Extensions

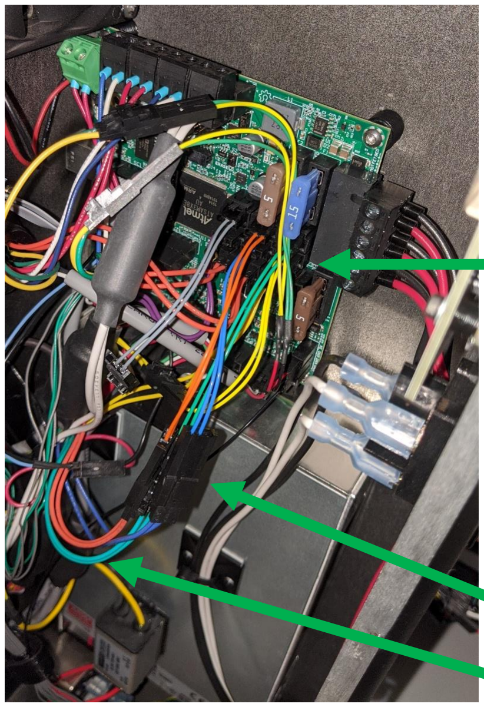
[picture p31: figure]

Lulzbot optimized cable lengths in their harnesses. As a result, some connections do not reach their intended target on the Archim2. The limit switches do not reach their new locations so extensions need to be made. This does not need to be done to all the limit switch connections as a few can be made to reach the Archim2 board, however, they make the wires tight. I just made an extension for all of them that were about 3.5” long and that provides plenty of slack.

## Limit Switch Connectors

## Extensions

## Original Cable Harness

# 5V AUX Connections

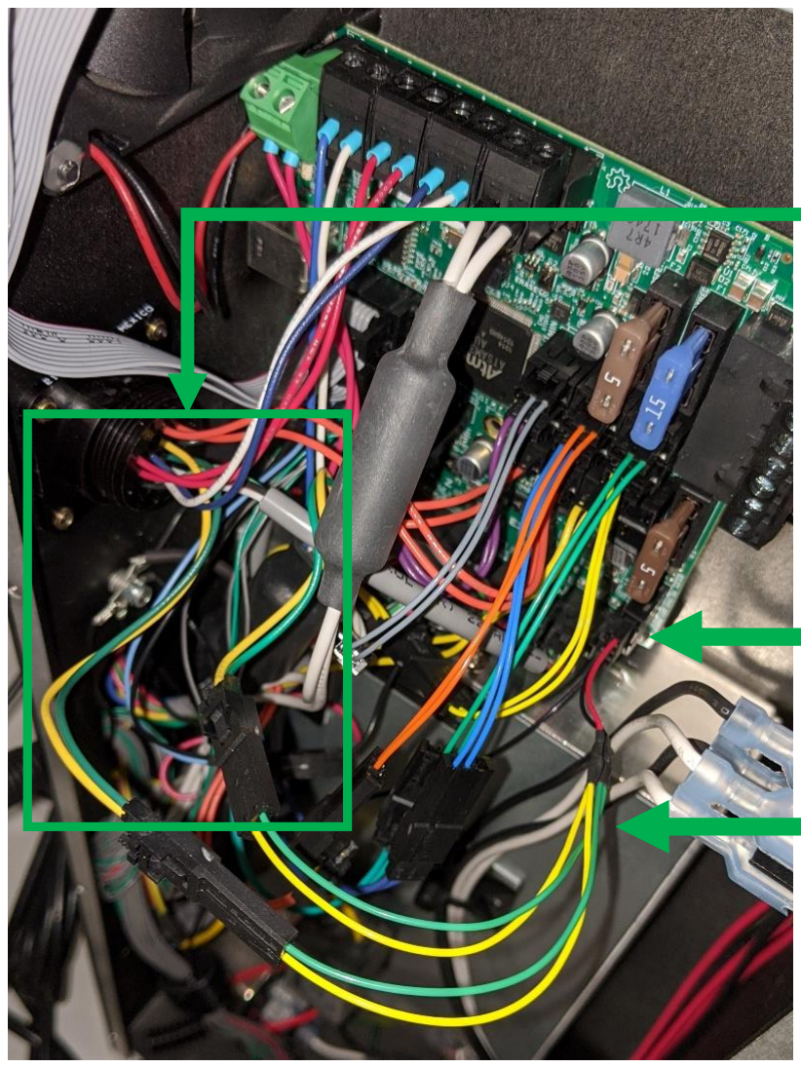
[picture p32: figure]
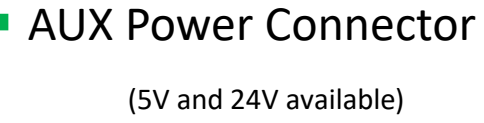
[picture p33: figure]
AUX Power Connector; (5V and 24V available)

The extruder heat break fan(s) need 5V to run. The Archim2 uses a 4 pin AUX connector that has 5V and VMT (supplied motor voltage = 24V on TAZ6). I wired the 5V supply (bottom right) to a “Y” cable that provides 5V to both of the extruder harnesses. Refer to the board layout on page 3 and wiring diagram in Appendix.

The stock wiring harness uses green and yellow wires for the fan 5V supply. The yellow wire is the 5V and green is ground. I wanted to keep both extrtuder harnesses wired up, so I tied both yellow wires together and both green wires together. This makes up the “Y” connection.

## 5V “Y” Cable

# Heater 1 Terminal Plug Replacement

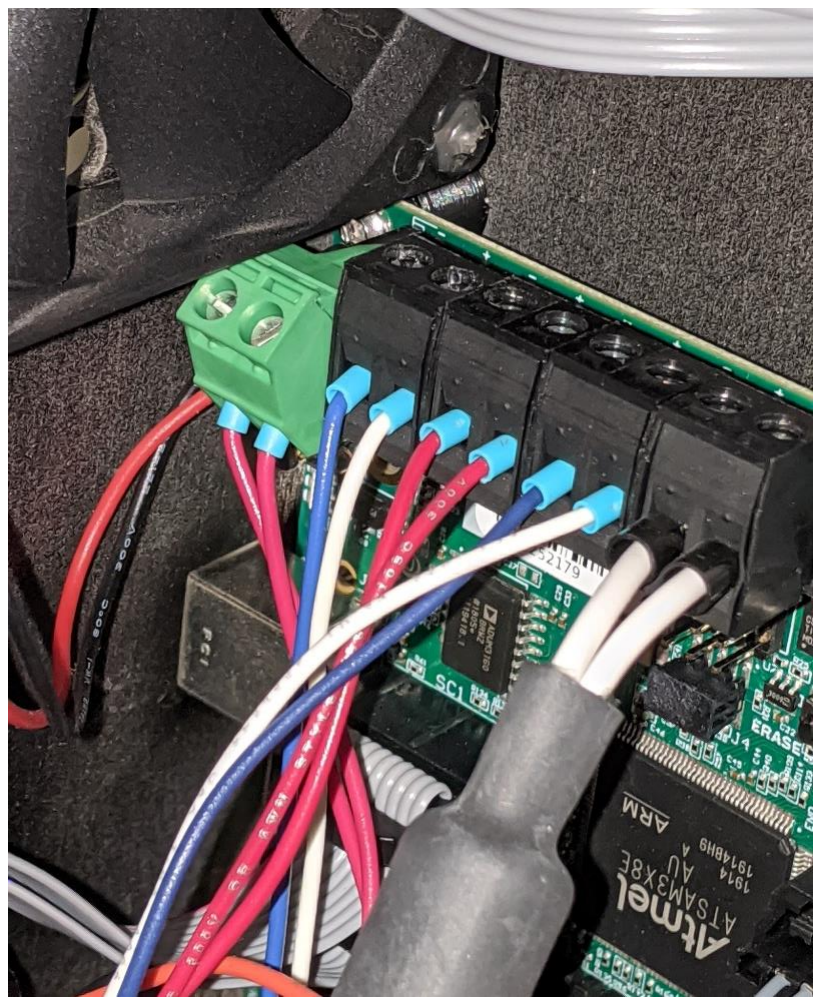
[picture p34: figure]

Replace the stock 90 degree black terminal block with one that allows for a 45 degree interface to clear the exhaust fan (green terminal plug in image). The terminal strip on the top of the Archim2 is right next to the edge of the board eliminating the clearance that the RAMBo board had.

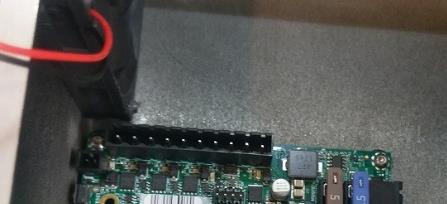
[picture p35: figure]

This shows how close the top terminal is to the top of the board and the interference that is created with the stock 90 degree terminal plug.

# Connector for GPIO Header

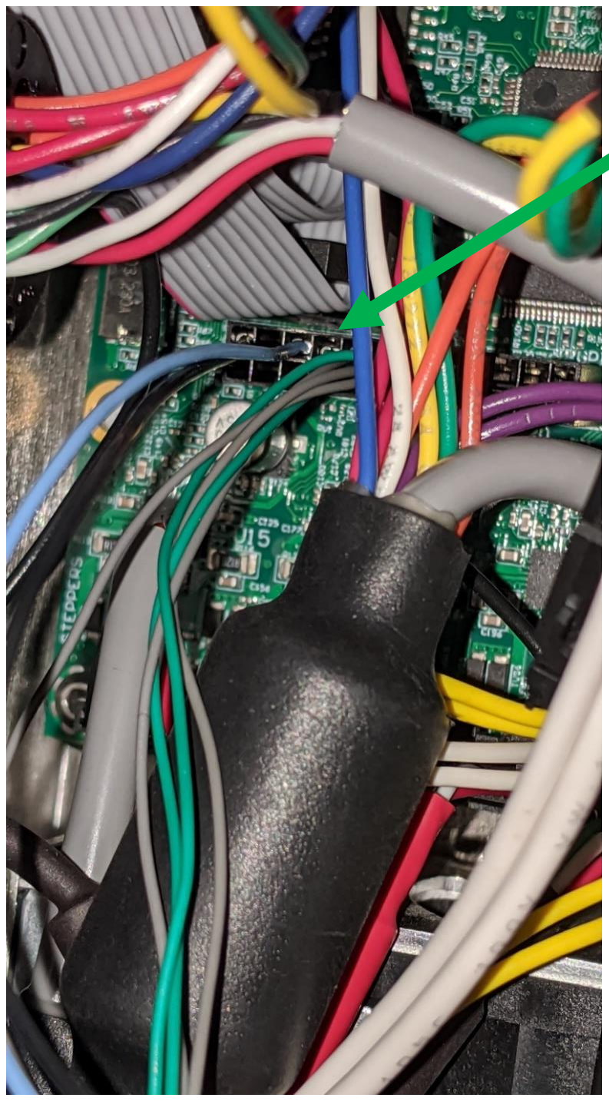
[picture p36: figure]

Use the GPIO header (J20) to wire in the bed leveling probe. The TAZ6 uses a 5V pulled up signal on the bed washers that gets grounded by the nozzle when contact is made using the RAMBo board. The RAMBo board had a 100nF capacitor wired between the signal and ground pins for this. (https://ohai.lulzbot.com/project/rambo_patch/taz-6/) I did not do that and have yet to have a problem with bed leveling. The Archim2 operates on 3.3V, thus we will now have a 3.3V pulled up signal on the bed washers. I used pin 19 on J20 (which routes to PB13 on the microcontroller) and pin 23 on J20 which is ground. See wire diagram in Appendix.

(Blue and Black wires used for bed probe in my setup)

# Connecting the Bed Level Probe

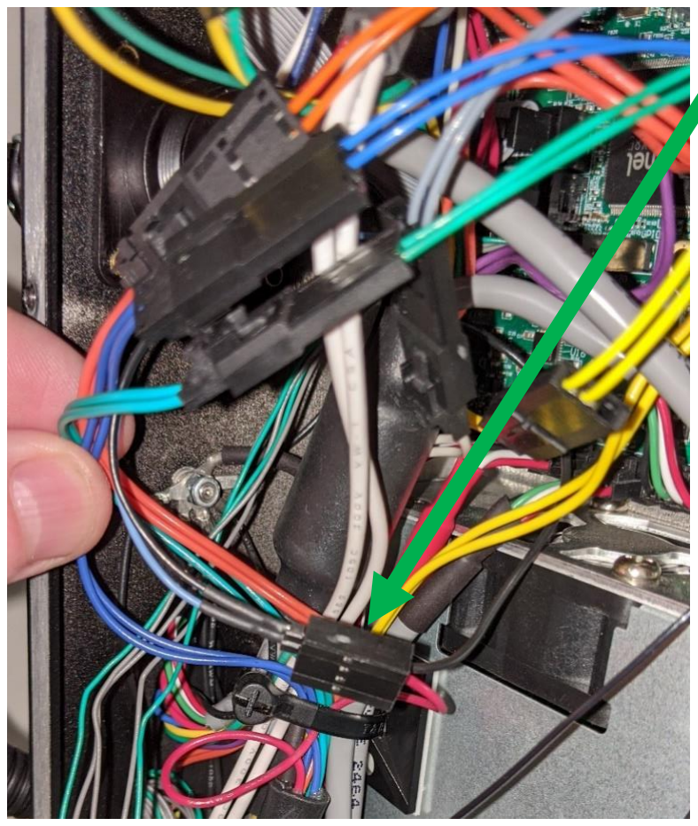
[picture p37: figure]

With the GPIO connector on the header, wire one of the GPIO pins and GND to the connector housing on the wiring harness. You have some flexibility here and can use any GPIO pin for this. On the TAZ6 wiring harness, the red wire is the pulled up 3.3V signal that gets routed to the bed washers, and the black is ground that runs to the heater block. For my installation, I wired the red wire to the light blue signal seen above which goes to pin 19 on the GPIO header (J20) and my firmware was set to match. The black wire is connected to pin 23 on J20, which is ground. The blue and black wires connected to the GPIO connector are soldered to a pair of header pins that connect to the bed level probe connector housing assembled into the TAZ6 harness. See wire diagram in Appendix.

Note: The RAMBo board operated on 5V, which means that the probe signal voltage was also 5V. The Archim2 operates at 3.3V, so the prove signal will also be 3.3V. This does not affect anything, but it is important to know that 5V signals should not be directly read by the microprocessor unless the pin is 5V tolerant – which is out of the scope of this guide.

Note for Drunken Octopus Users: Drunken Octopus Firmware uses pin 20 (not 19) for the bed washers. If using that Drunken Octopus firmware, use pin 20 instead of pin 19.

# LCD Screen Wiring

The connectors in the Archim2 board that support the stock TAZ6 LCD screen are labeled SC1 and SC2. They are the same pinout as the RAMBo 1.4 PCB. Thus, if your TAZ6 came with the 1.4 version of the RAMBo board, you can just connect EXT1 and EXT2 to SC1 and SC2 respectively*. If your TAZ6 came with the older RAMBo 1.3L (like mine did) you will have to get a set of 10 pin, 0.1” pitch IDC cables. I got some 30cm long cables that allow me to connect the LCD to the Archim2 while routing them along the roof of the case and not impede airflow. Try to get cables with keyed connectors so you don’t accidently plug them in backwards. Looking at the Archim2 board, pin 1 of the LCD connectors is on the left, so the red stripe on the cable should also be on the left.

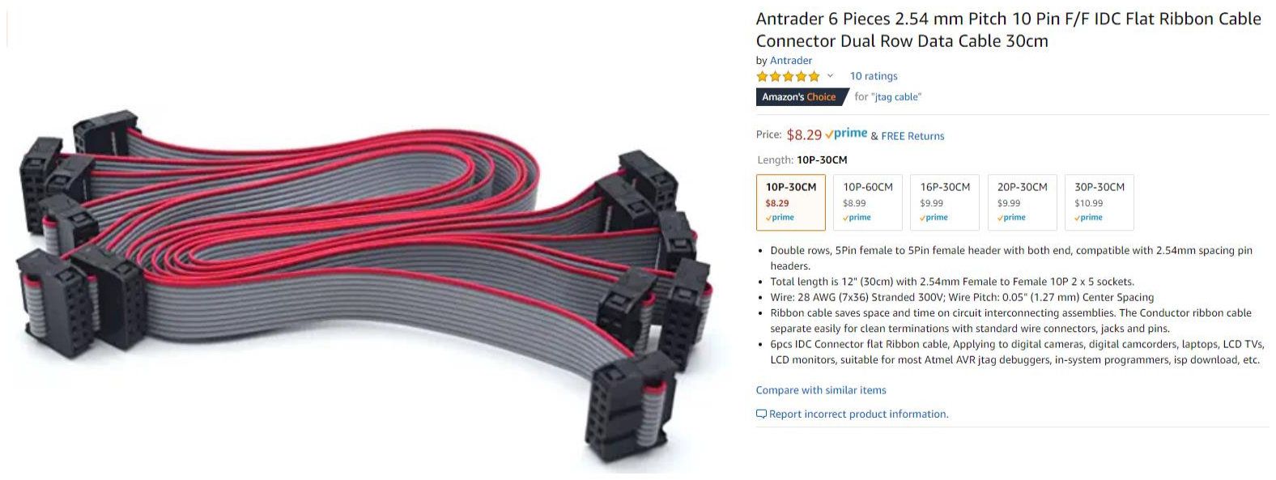
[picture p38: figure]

*Note: I am unsure if the length of the stock 10 pin cables that come with the RAMBo 1.4 version of the TAZ6 are long enough to reach the LCD connectors on the Archim2. Even if they are, then might not be ideal for airflow.

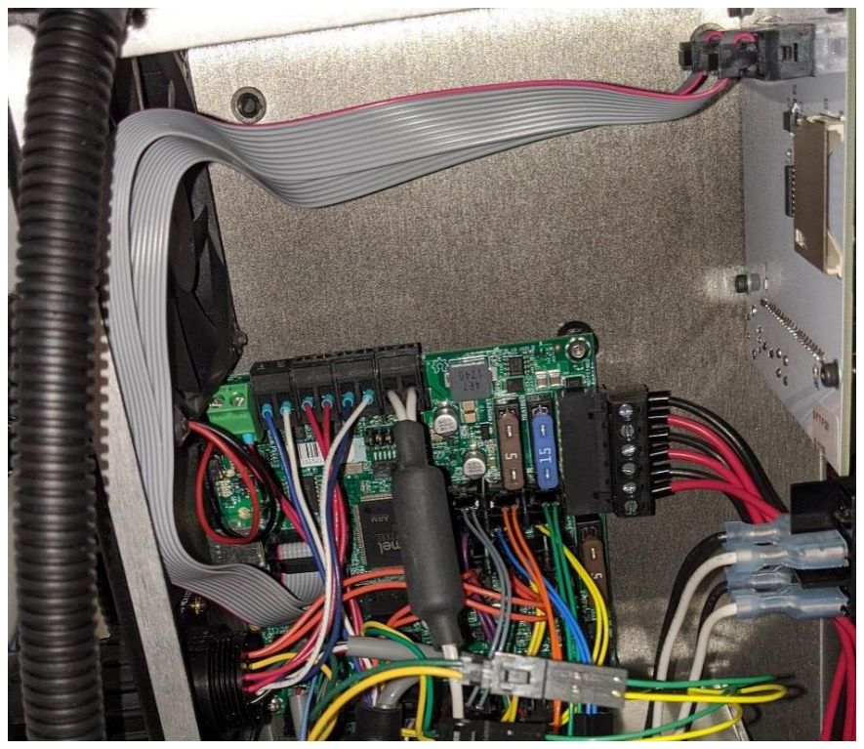
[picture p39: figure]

Cables installed with red stripe (pin 1) on the left side for both connectors.

# Mechanical

This section covers the mechanical considerations for the conversion, which is based on the assembly of the Lulzbot TAZ Pro. (https://ohai.lulzbot.com/project/control-box-assembly/quiver/) The TAZ Pro also uses the Archim2 board and Lulzbot has installed a heatsink bar that allows for a heat path from the stepper controllers to the control box housing. The heatsink bar is made from aluminum and sandwiched between two sheets of thermal heat pads. The thermal heat pads allow for optimal heat transfer while maintaining electrical isolation between the board and the case.

# Heatsink Mount

The heatsink stack up is held in place with the use of a 3D printed mount that registers itself using the PCB standoffs. The STL of the stock heatsink mount is provided, as well as a modified version that provides for a longer heatsink bar. The stock mount only supports a heatsink bar that sits under the X, Y, and Z stepper controllers. I am not sure why this design excludes the E0 and E1 stepper controllers, so I modified the mount to allow for a longer heatsink bar that sits under all 5 stepper controllers, which is also included in this document. I used ABS incase it got warmer than expected. Didn’t want it sagging.

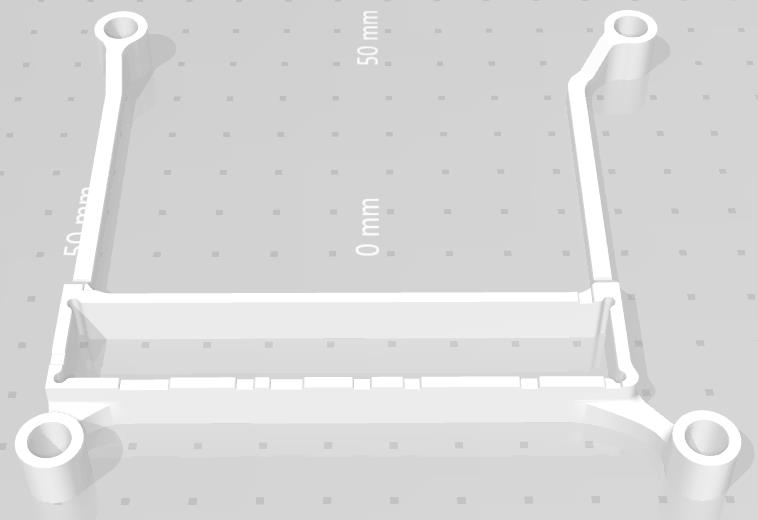
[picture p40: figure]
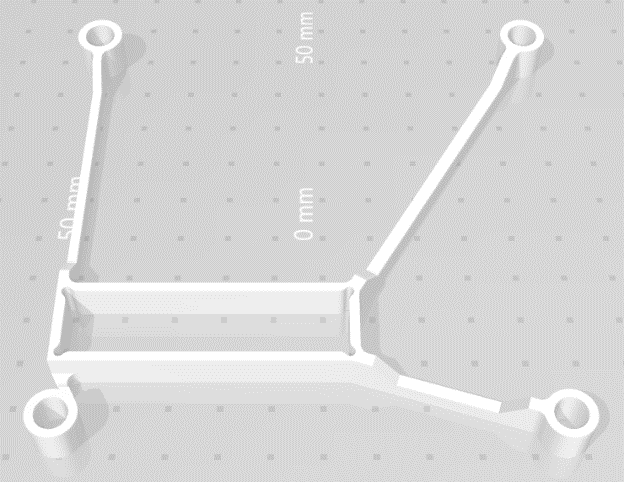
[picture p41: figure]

Stock heatsink mount (only covers XYZ) | Modified heatsink mount (covers all controllers)

Below shows the heatsink mount installed with the aluminum bar. Under the aluminum bar is a 0.5mm thick strip of thermal gap pad described below. A 1.0mm thick gap pad is placed on top of the aluminum bar and the board is installed.

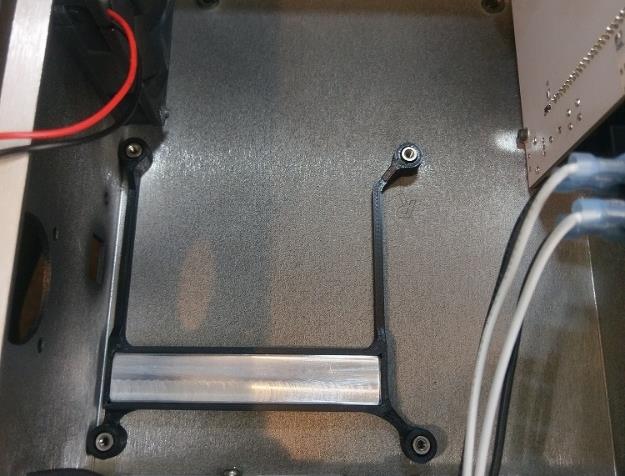
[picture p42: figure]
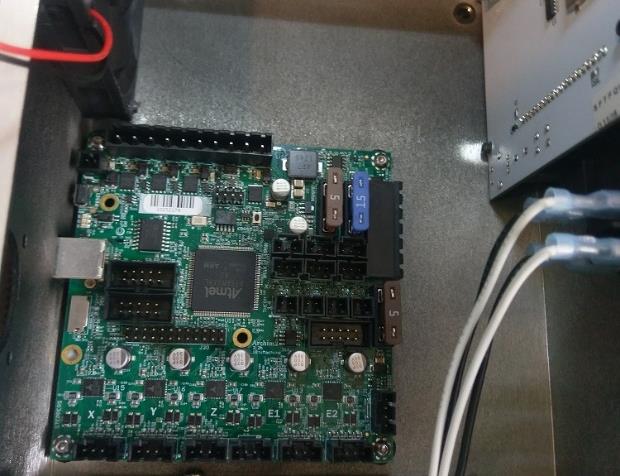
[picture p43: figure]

Installation of the modified mount | Board installed over modified mount

# Heatsink Bar

The stock heatsink bar is 55mm long (refer to the included PDF). The modified heatsink bar is 85mm long and all other dimensions are the same as the stock heatsink bar. Please note that it is
recommended to measure the height of the PCB standoffs in your printer. Since the height of these are not a critical dimension in the TAZ6, it is conservable that they may vary slightly between printer revisions and build lots. The standoff height dimension is an important factor in the thickness requirement of the aluminum heatsink. It needs to be sized such that the board applies slight compression of the thermal pads when screwed down so that the pads can conduct the heat, but not so much that the PCB gets aggressively bowed. See included PDF or Appendix and next section for heatsink bar height calculation based on thermal pad thicknesses.

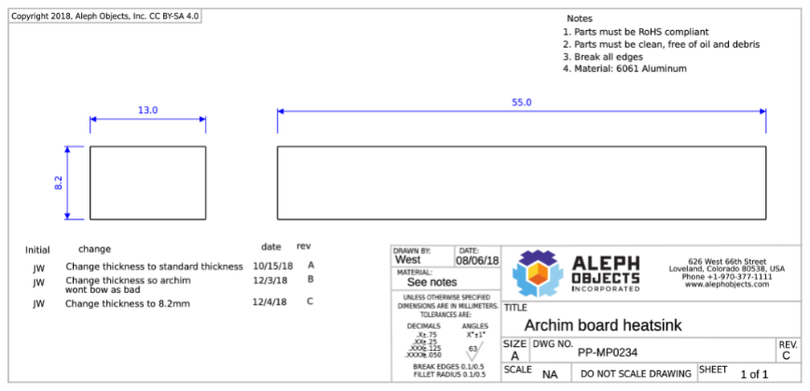
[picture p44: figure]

## Heatsinking Alternatives (Use Caution)

Use at your own risk! While this may be a viable alternative, I have not tested this!

An alternative heatsinking method may be desired if access to the equipment needed to manufacture an aluminum bar to the proper dimensions is not available. Small heatsinks (like the ones used on things like Raspberry Pi’s, etc.) with thermal adhesive has been discussed from time to time and may be a viable alternative. There are some things to consider:

1. Is the heatsink capable of providing enough cooling? Does it have enough mass and convection capability?
2. Does it use real thermal adhesive? I have seen many (and fallen victim to some myself) that claim to use thermal adhesive, but use cheap double-sided tape which actually acts like an insulator!
3. Is the adhesive strong enough to keep the heatsink from falling off? The TMC controllers can get very hot and this may cause an adhesive holding a heatsink vertically to lose adhesion. The controllers also have a small surface area, so there is little to stick too to begin with.

The other thing to consider is that the heatsinks will need active airflow to do their job effectively. Avoid running the electronics with the enclosure open as this will cause the exhaust fan to just cycle air around the top and not pull it from the bottom vent and across the heatsinks.

# Thermal Pads

For the thermal pads, I used Fujipoly thermal pads to interface the aluminum heatsink between the PCB and the case. This stuff isn’t cheap, but it has great thermal conductivity and electrical isolation characteristics. I used 0.5mm thick material on the bottom (where the heatsink interfaces with the case) and 1.0mm thick material on the top (where the heatsink interfaces with the PCB). The reasoning for this was to allow for easier deformation of the material against the more fragile PCB and the slightly thicker material allowed for this. The datasheet for this material indicates that 20% compression will yield the best results. I tried to accommodate this by adjusting the heatsink bar height.

In my printer, the PCB standoffs are exactly 10mm. With a 0.5mm bottom pad and a 1.0mm top pad, I had a total of 1.5mm of pad height. 20% of that is 0.3mm, so I wanted a heatsink stack up of 10.3mm. I calculated the heatsink bar height using 10.3mm as the final stack up dimension which included up to 0.3mm of compression. I also cut the pads the same size as the aluminum bar so that they fit inside the mount preventing the mount from applying compression.

My heatsink bar is then calculated as:

(total stack up) - (thickness of bottom pad) - (thickness of top pad) = (heatsink bar height)

=> 10.3mm - 0.5mm - 1.0mm = 8.8mm

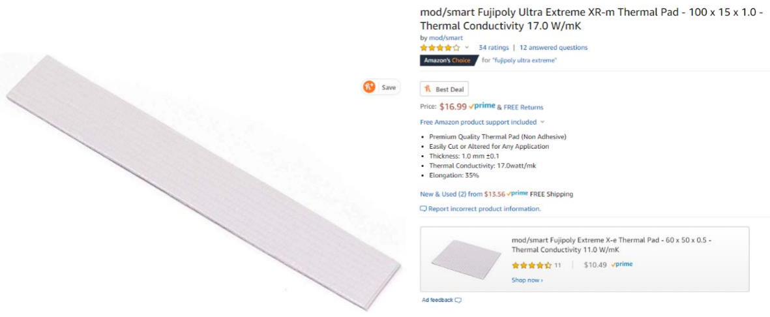
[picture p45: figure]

Clean the case where the thermal pad will interface with and the heatsink bar with alcohol. Take care when installing the board after placing the top pad. You should have a good idea if the heatsink bar is the proper height based on how it wants to rest. I fastened the two top board screws first and checked that the bottom of the board needed light pressure to touch the standoffs. This indicates that there will be compressive force on the heatsink stack up. I also pressed hard on the heatsink bar to compress the bottom pad before installing the top pad and the board. You don’t want too much compressive force supplied by the board as it could cause the board to bow. Once the board was tightened down, I gently pressed on each of the motor controllers to ensure the board area under them interfaced with the pad thoroughly. ESD precautions should be in effect while doing this!

# Configuration

After completing all the electrical and mechanical modifications and the board is fully installed - double check all electrical connections! All the connections (except the bed level probe and AUX 5V for the heat break fans) are a direct swap, pin-for-pin from the RAMBo board. This includes power plugs and FET controlled outputs. The pin that was selected as the bed level probe signal will need to be defined as an active low, pulled-up signal in the firmware as the bed level probe pin. This means that the microprocessor on the Archim2 board will read 3.3V while the nozzle is not touching one of the bed washers and this condition will be interpreted as a false state. Once the nozzle touches one of the washers, a path to ground for the bed level signal will be created and the microprocessor will read 0V, which will be interpreted as a true state.

Note: Proceed with caution. Ensure that any pins that are used as signals (like the bed level probe) are defined properly using a pull-up resistor in the firmware (or externally if internal pull-ups are not supported, which I do not think is the case for the microcontroller used on the Archim2). If a pin is configured as an output and set high, grounding it could damage the microcontroller.

Other peripherals, such as filament sensors, lighting control, external fans, etc, can be wired to the GPIO header and written into the firmware as needed. Refer to the Archim2 schematic (https://github.com/ultimachine/Archim/blob/c68ed12ccc4da3c50be3b65031d0f8b64b89efce/Project%20Outputs/Archim2_2.1a_Schematic.PDF) from the reprap wiki. (https://reprap.org/wiki/Archim2)

# Firmware

This could have multiple options, but below are the two that I think are best supported.

Marlin Option: If using Marlin is desired, Drunken Octopus (https://github.com/marciot/drunken-octopus-marlin) states that this configuration is supported. I have not done this yet, but it seems like the best Marlin path. Thanks Marcio! Please note that Drunken Octopus has the bed washers configured on pin 20 of J20. Ensure your wiring is correct for this firmware.

Klipper Option: I have created a Klipper (https://github.com/KevinOConnor/klipper) configuration file for my TAZ6 Archim2 with Dual v3 extruder printer. It has all the configuration needed, including the probe pin defined on pin PB13 as a pulled-up, active low signal. I have been experimenting with this for a few months and have had no operational problems. I will soon add it to the Klipper repo so others can use it out of the box with Klipper!

Disclaimer: You do this work at your own risk. Your warranty will likely be voided by doing this. It is up to the implementer if the advantages of doing this work outweigh the risks. I have not run this configuration with Marlin firmware yet, so there may be other needed modifications if using that codebase, although I cannot think of any. I use Klipper firmware to run my printer currently and it allows for custom pin definition in a configuration file. This was done for the bed leveling probe using the GPIO header.

14

# APPENDIX

# Digikey Parts BOM

Below is the list of parts that are needed to complete the electrical work outlined in this document.

Index | Quantity | Part Number | Manufacturer Part Number | Description | Use
1 | 1 | WM2902-ND | 0050579404 | CONN HOUSING 4POS .100 W/LATCH | Aux Power connector for 5V to extruder heat break fan
2 | 50 | WM2510CT-ND | 0016020086 | CONN SOCKET 22-24AWG CRIMP TIN | Female crimps for limit switch extensions and Aux power
3 | 50 | WM2517CT-ND | 0016020107 | CONN PIN 22-24AWG CRIMP TIN | Male crimps for limit switch extensions
4 | 6 | WM2901-ND | 0050579403 | CONN HOUSING 3POS .100 W/LATCH | Female connector for limit switch extensions
5 | 6 | WM2534-ND | 0701070002 | CONN HOUSING MALE 3POS .100 | Male connector for limit switch extensions
6 | 1 | 23-0022552241-ND | 0022552241 | CONN HOUSING 24POS .100 DUAL | GPIO connector housing block
7 | 50 | WM14366CT-ND | 0700580086 | CONN SOCKET 22-24AWG CRIMP TIN | Crimps for GPIO housing block
9 | 1 | 277-5963-ND | 1826283 | TERM BLOCK PLUG 2POS 5.08MM | 45 deg terminal plug to clear exhaust fan
10 | 2 | WM2533-ND | 701070001 | CONN HOUSING MALE 2POS .100 | Male connector for 5V AUZ power to heat break fans
11 | 1 | WM50032-24-ND | 22284242 | CONN HEADER VERT 24POS 2.54MM | Header pins to connect to bed level probe harness

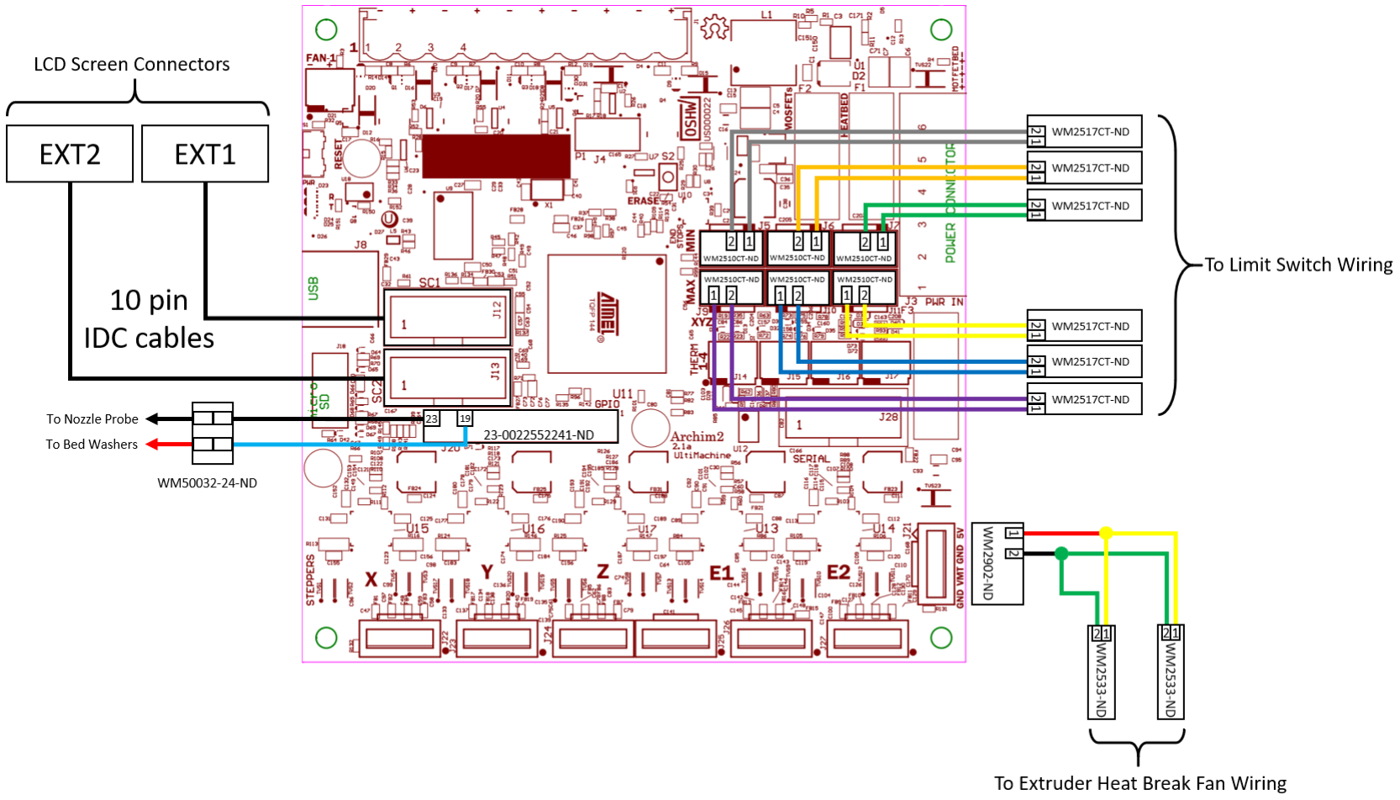
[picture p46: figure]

15

# Wiring Diagram

16

# Aluminum Heatsink Mechanical Drawing


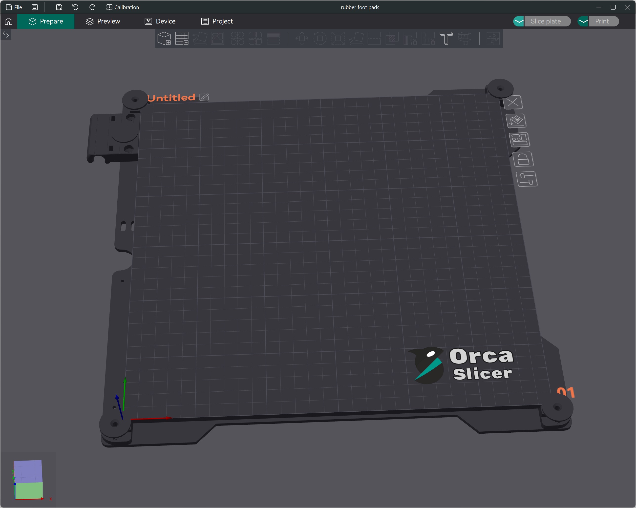
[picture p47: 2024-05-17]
TAZ6_Project/Orca Slicer TAZ 6 Print Bed Image.jpg

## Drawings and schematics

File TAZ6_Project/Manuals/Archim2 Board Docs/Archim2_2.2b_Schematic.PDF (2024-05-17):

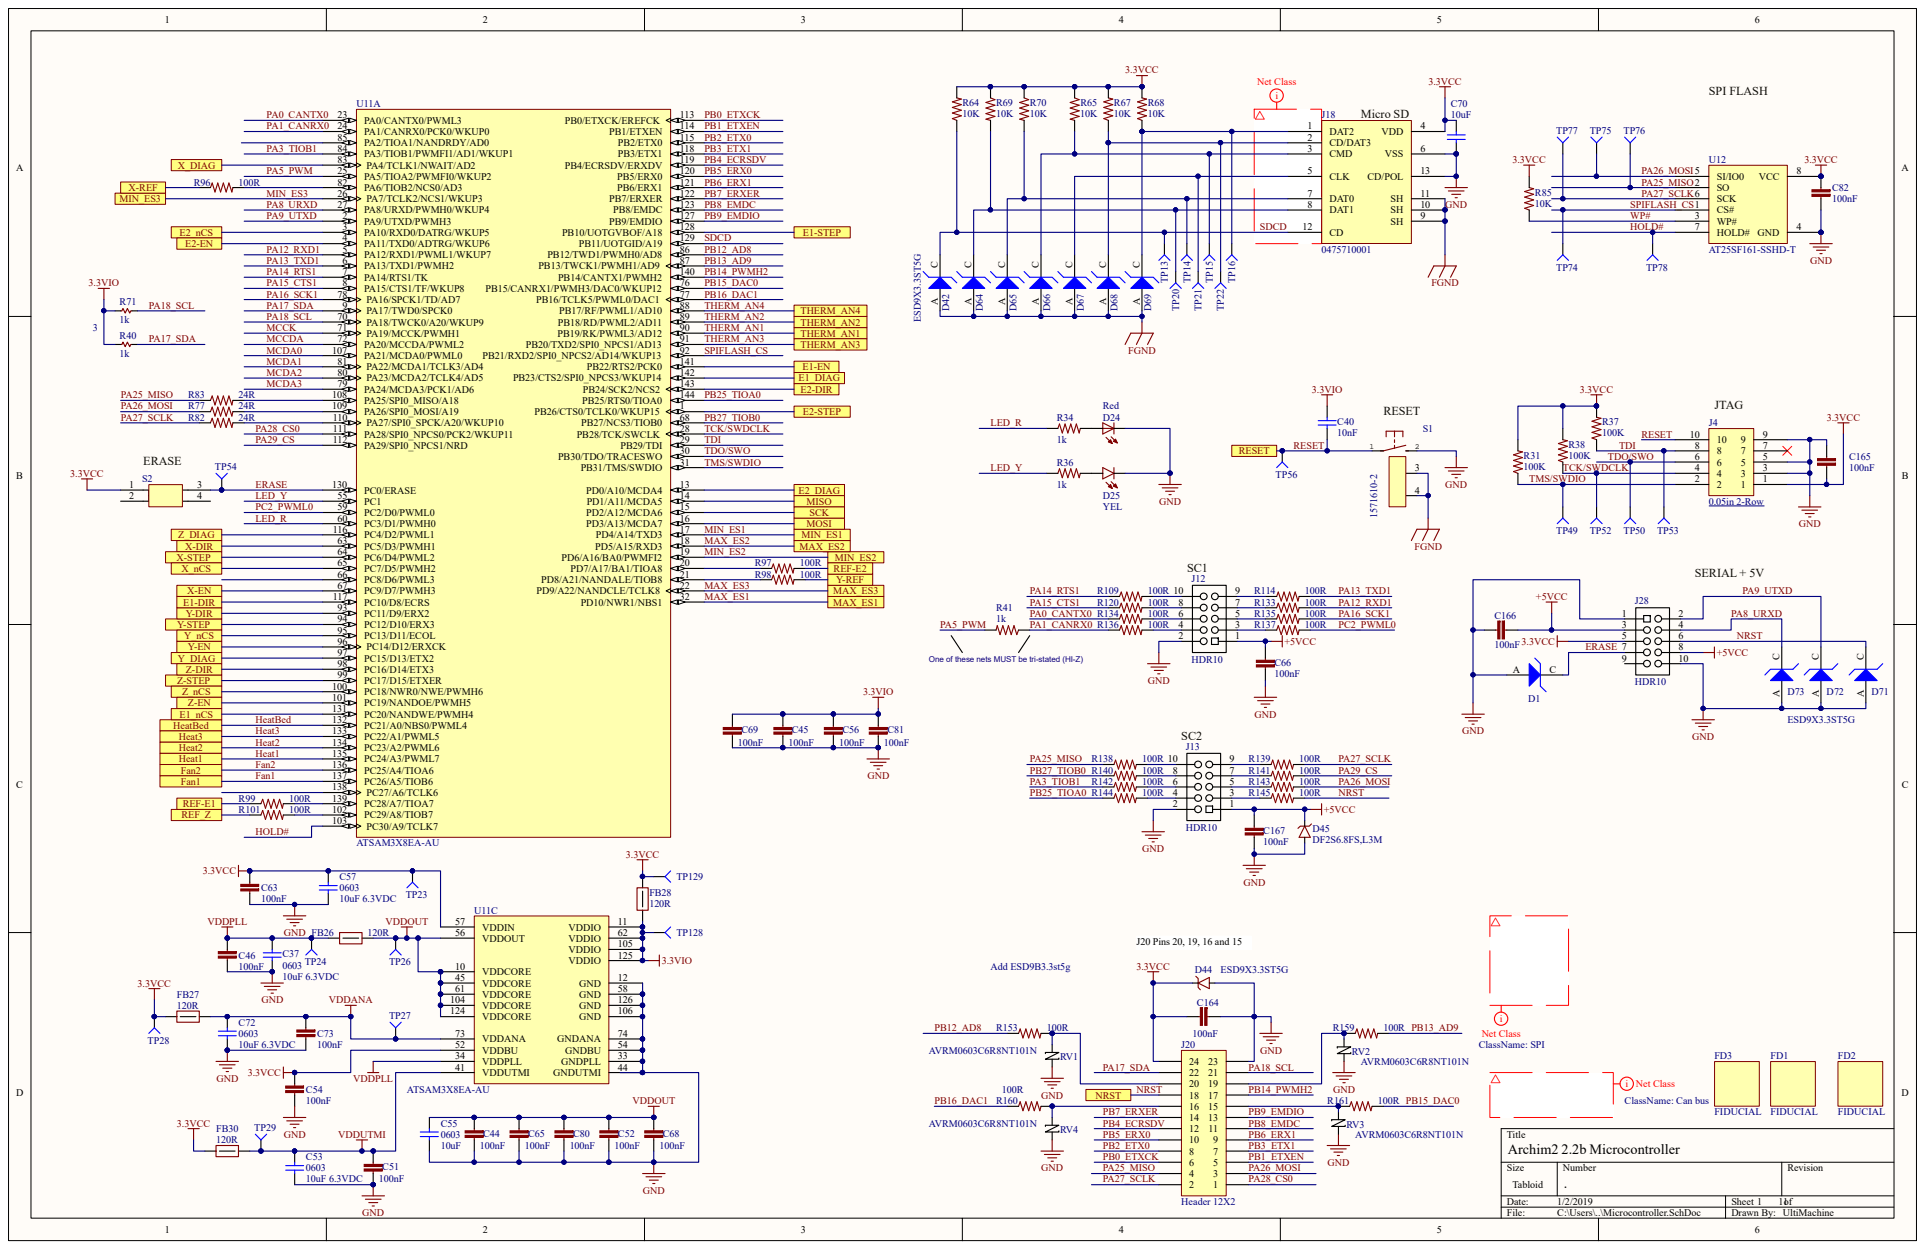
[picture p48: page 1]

## Input Compatible with 12-24VDC

## +3.3V DCDC Regulator +5V DCDC Regulator (Aux)

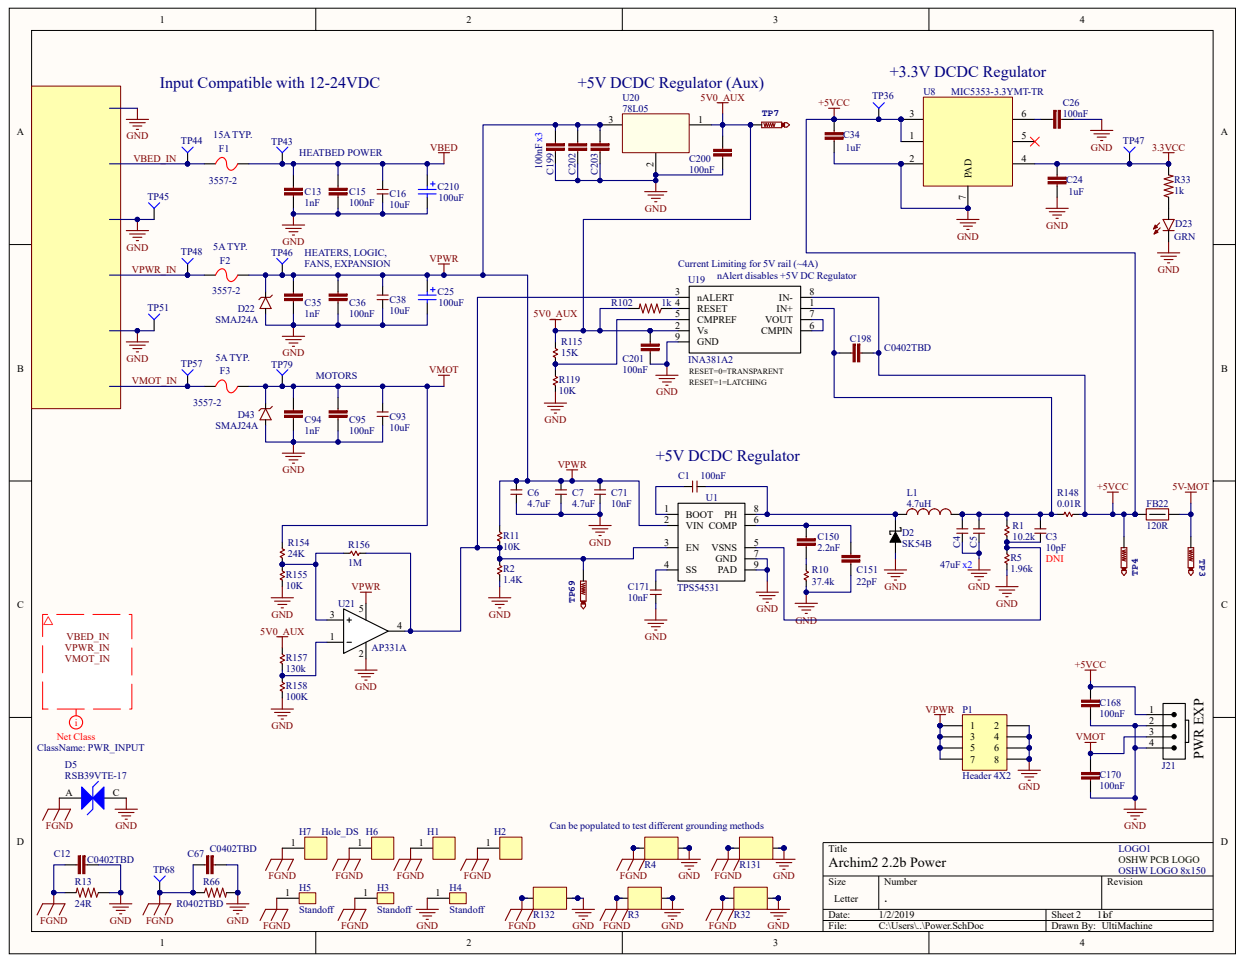
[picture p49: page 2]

Current Limiting for 5V rail (~4A)

nAlert disables +5V DC Regulator

Can be populated to test different grounding methods

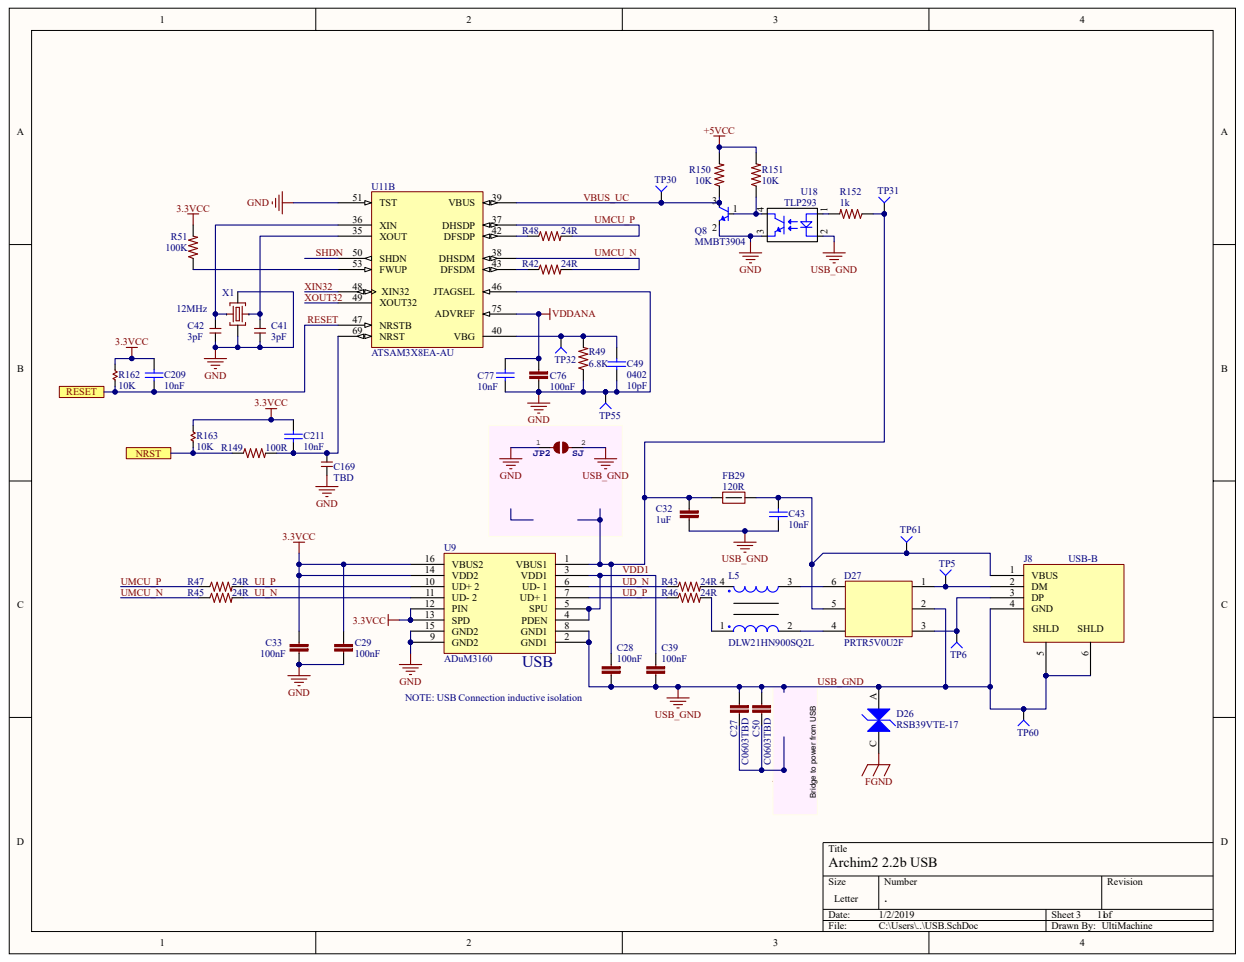
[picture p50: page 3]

GND
Bridge to power from USB

NOTE: USB Connection inductive isolation GND

# End Stop Channels

X

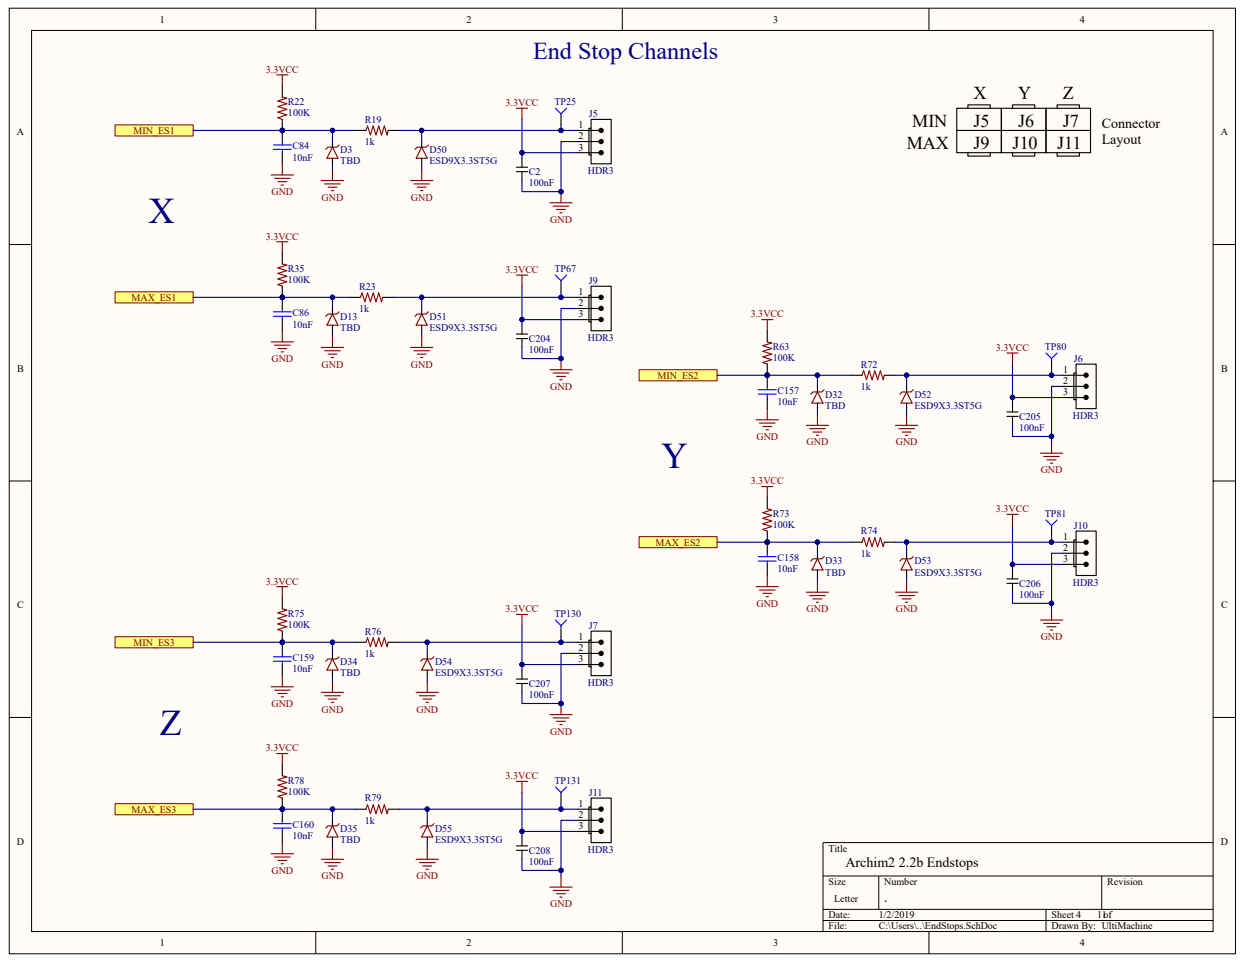
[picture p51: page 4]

# Motor-X

X | Y | Z | E1 | E2

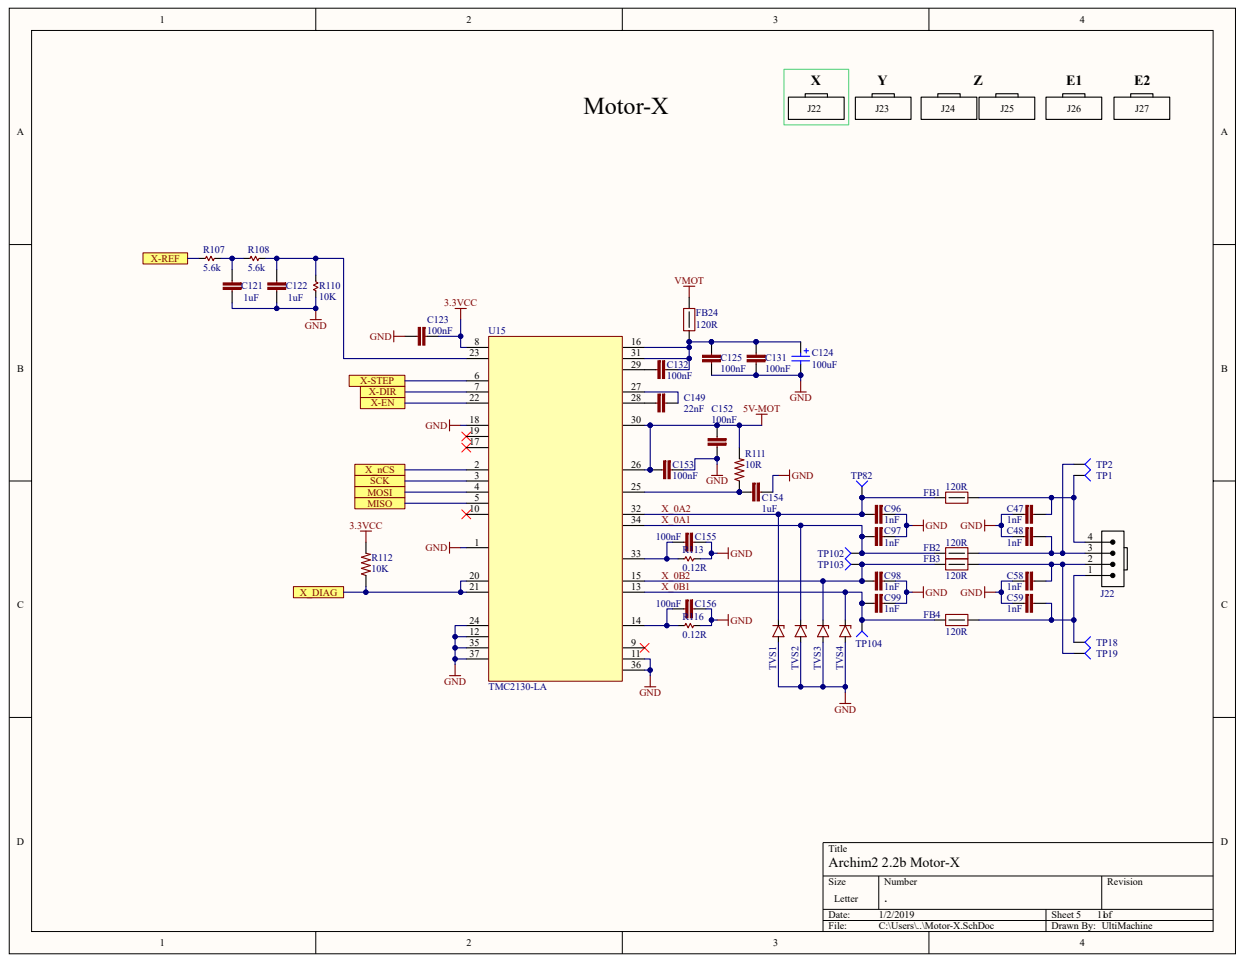
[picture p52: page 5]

# Motor-Y

X | Y | Z | E1 | E2

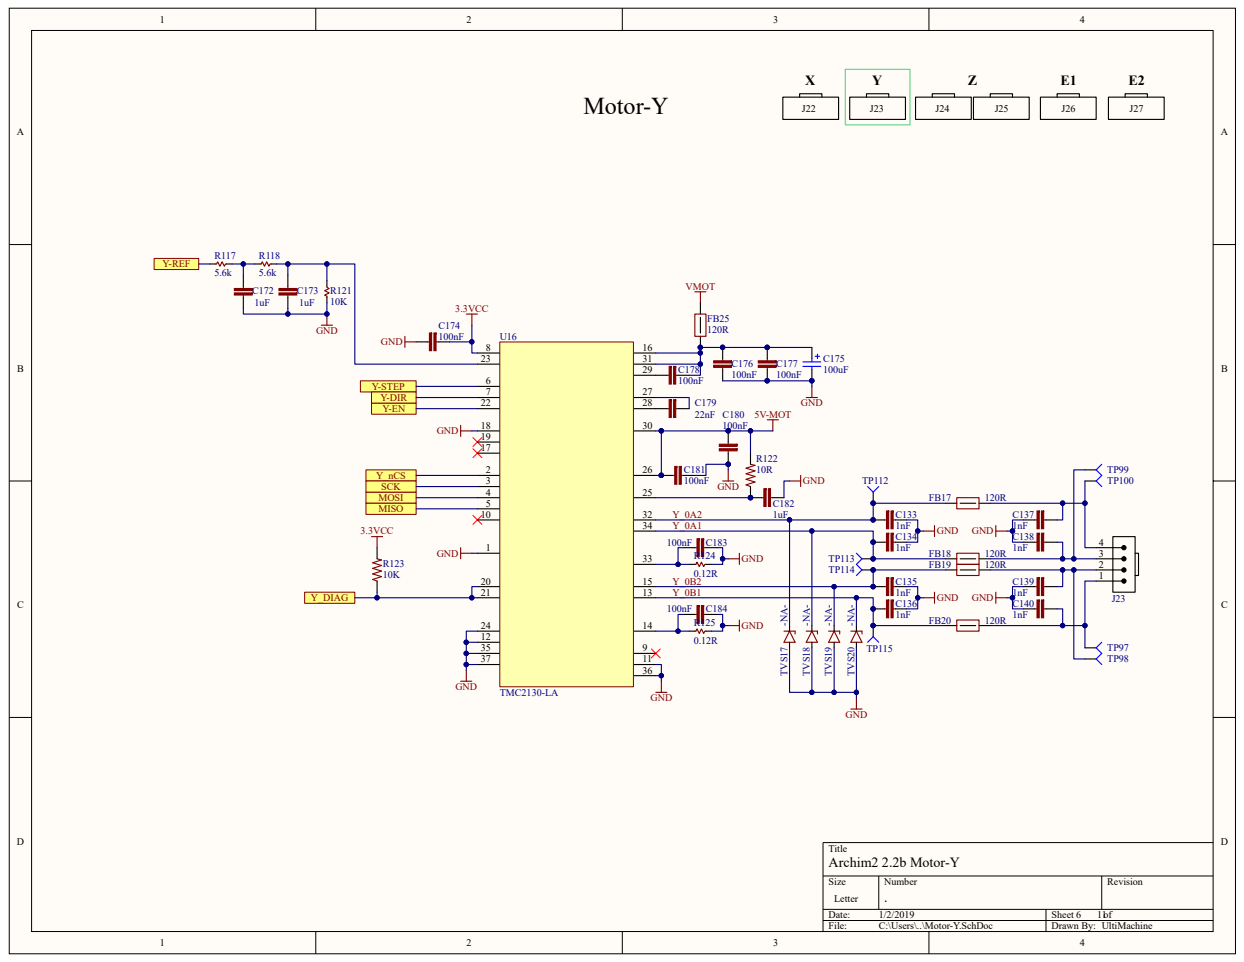
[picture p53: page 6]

# Motor-Z

X | Y | Z | E1 | E2

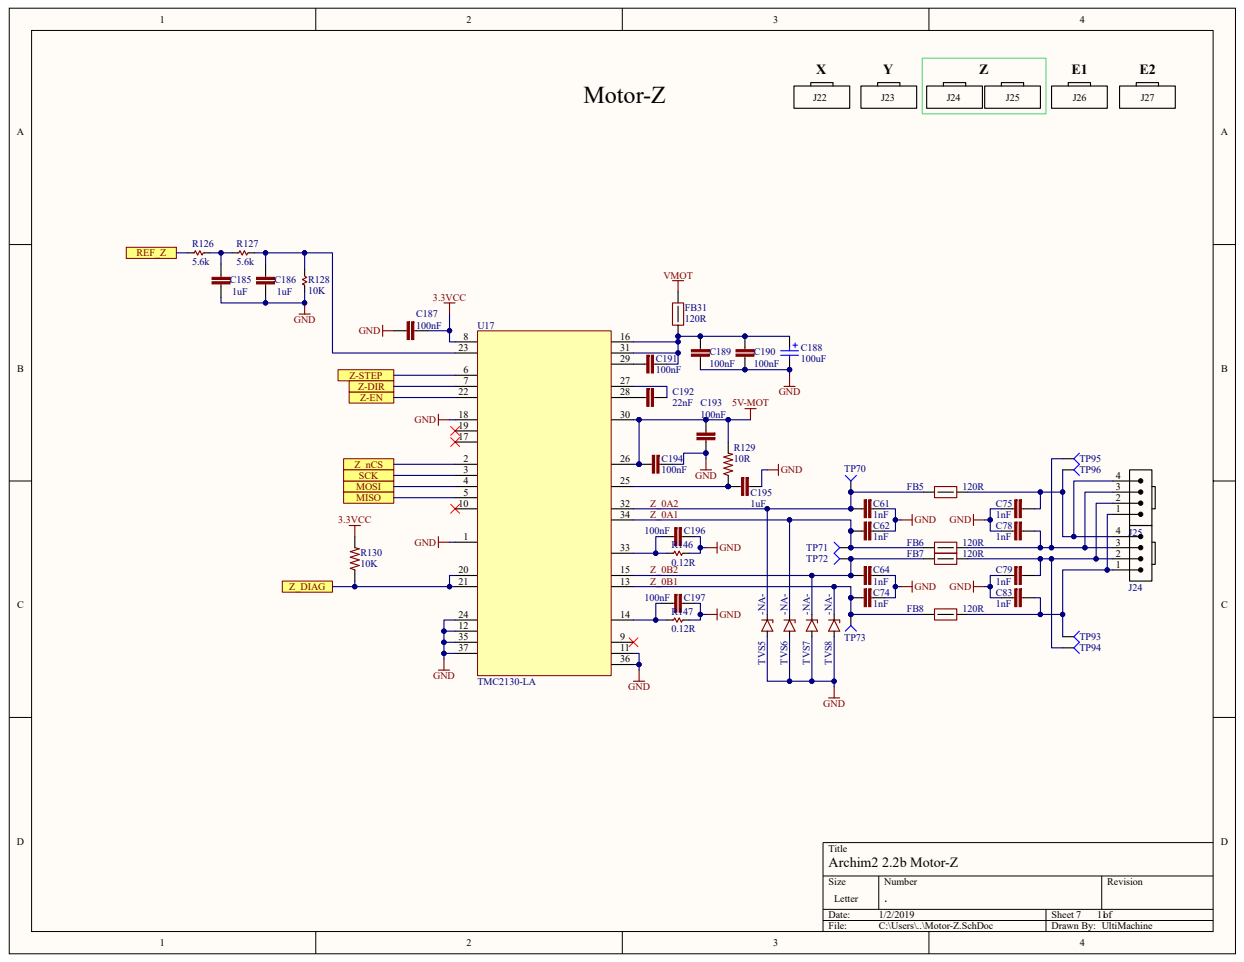
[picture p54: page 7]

# Motor-E1

X | Y | Z | E1 | E2

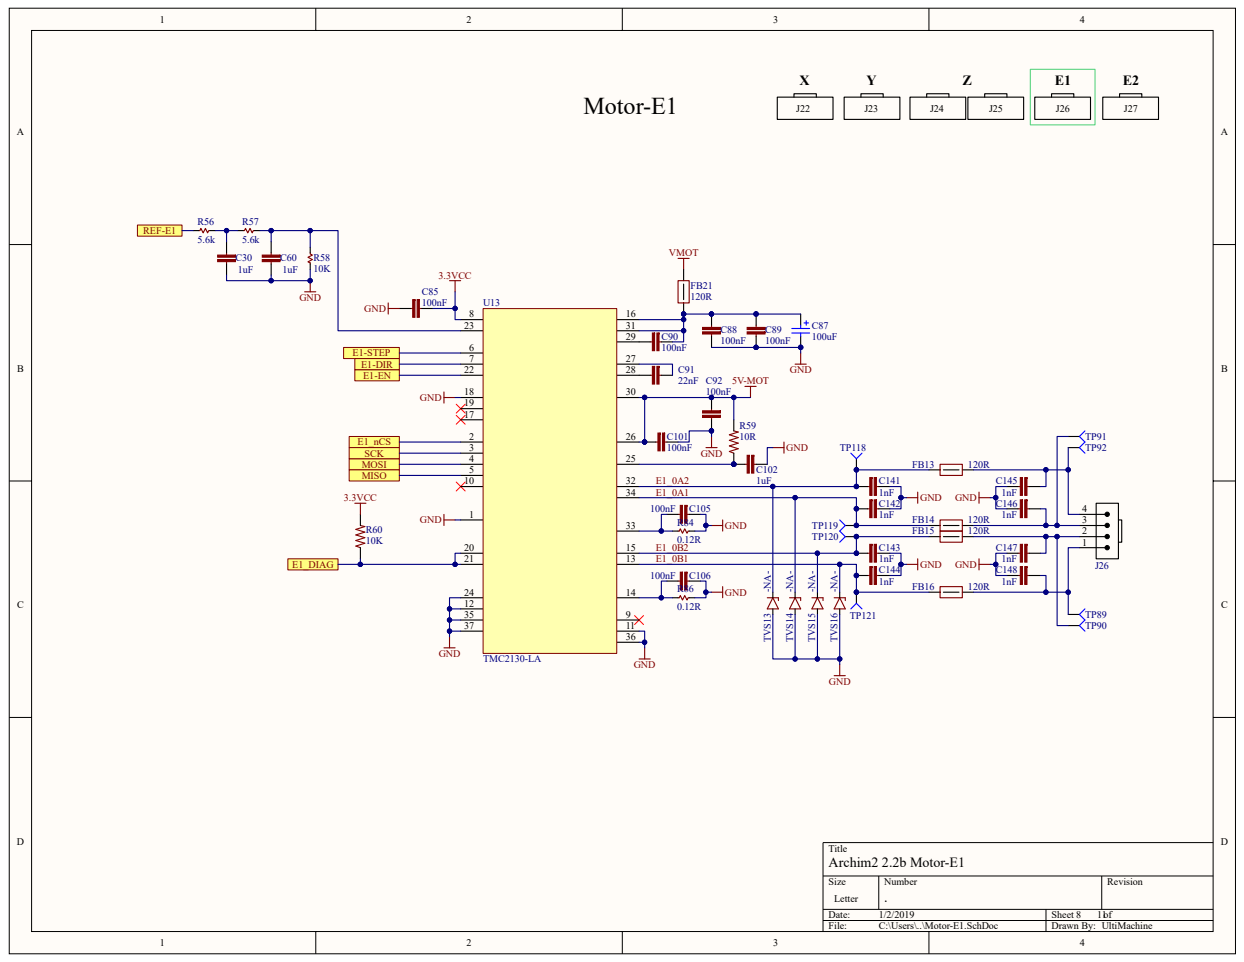
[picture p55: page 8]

# Motor-E2

X | Y | Z | E1 | E2

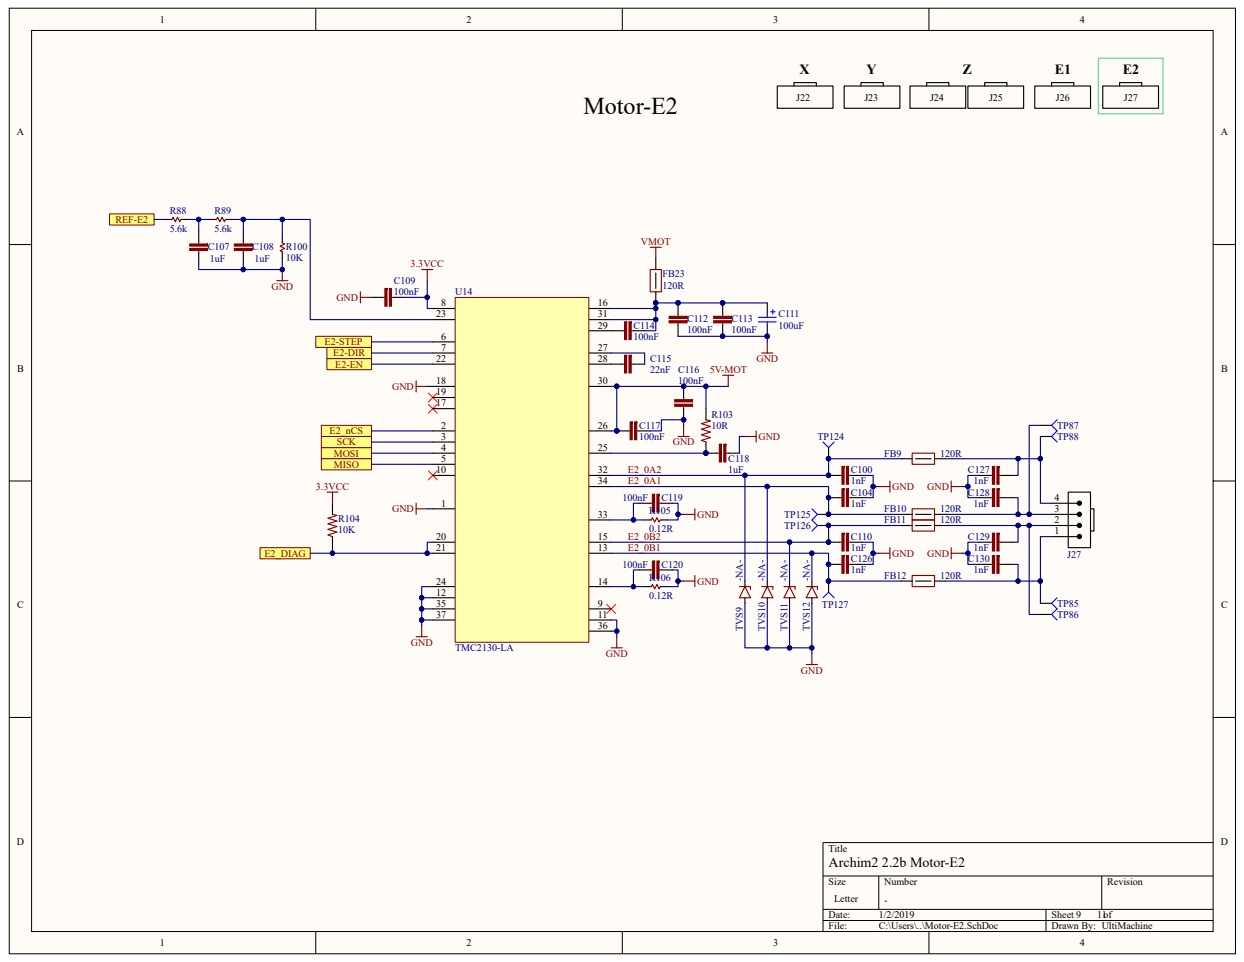
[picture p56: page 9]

# Thermistor Channels

## Thermistor Connector

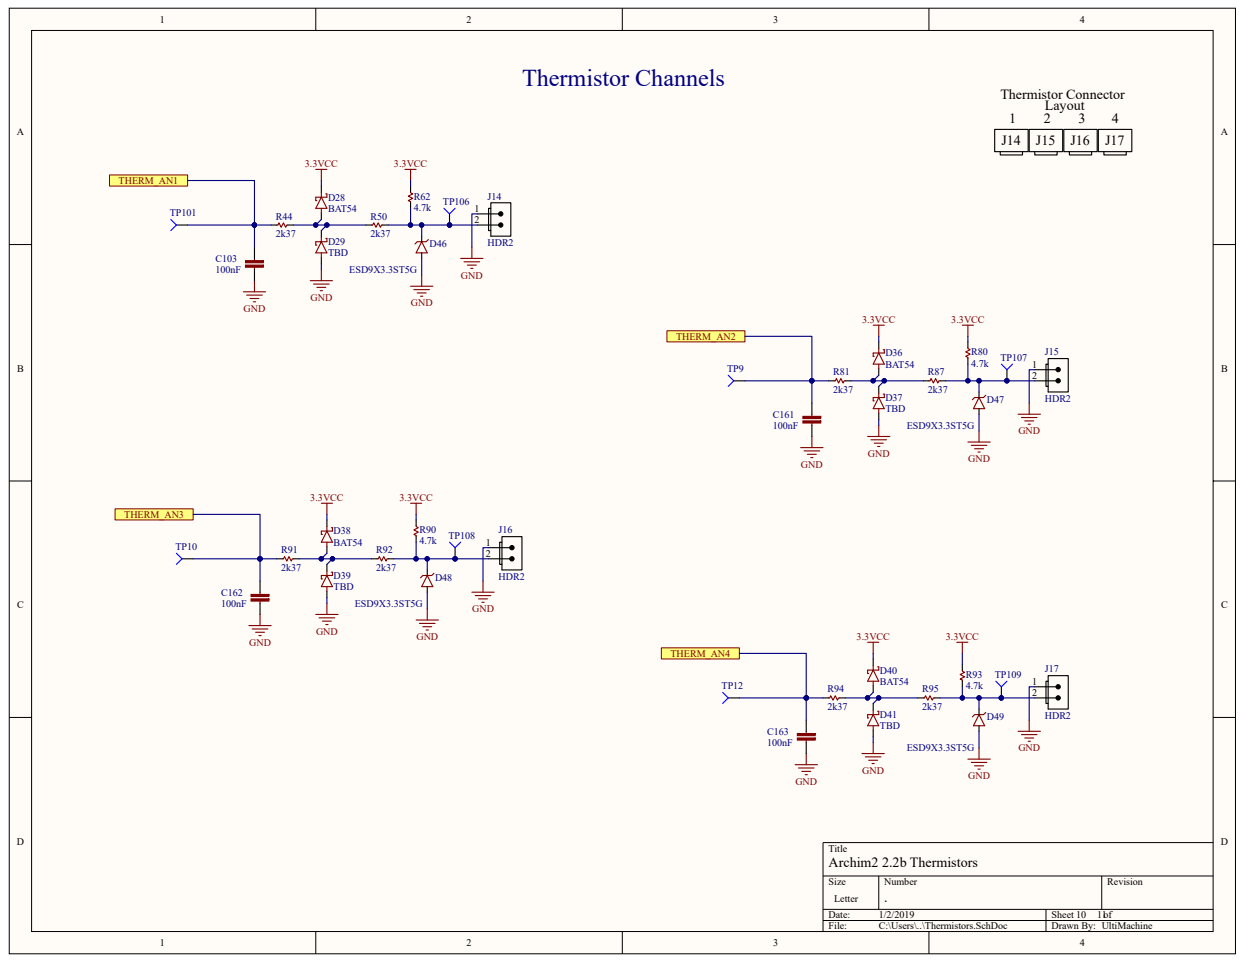
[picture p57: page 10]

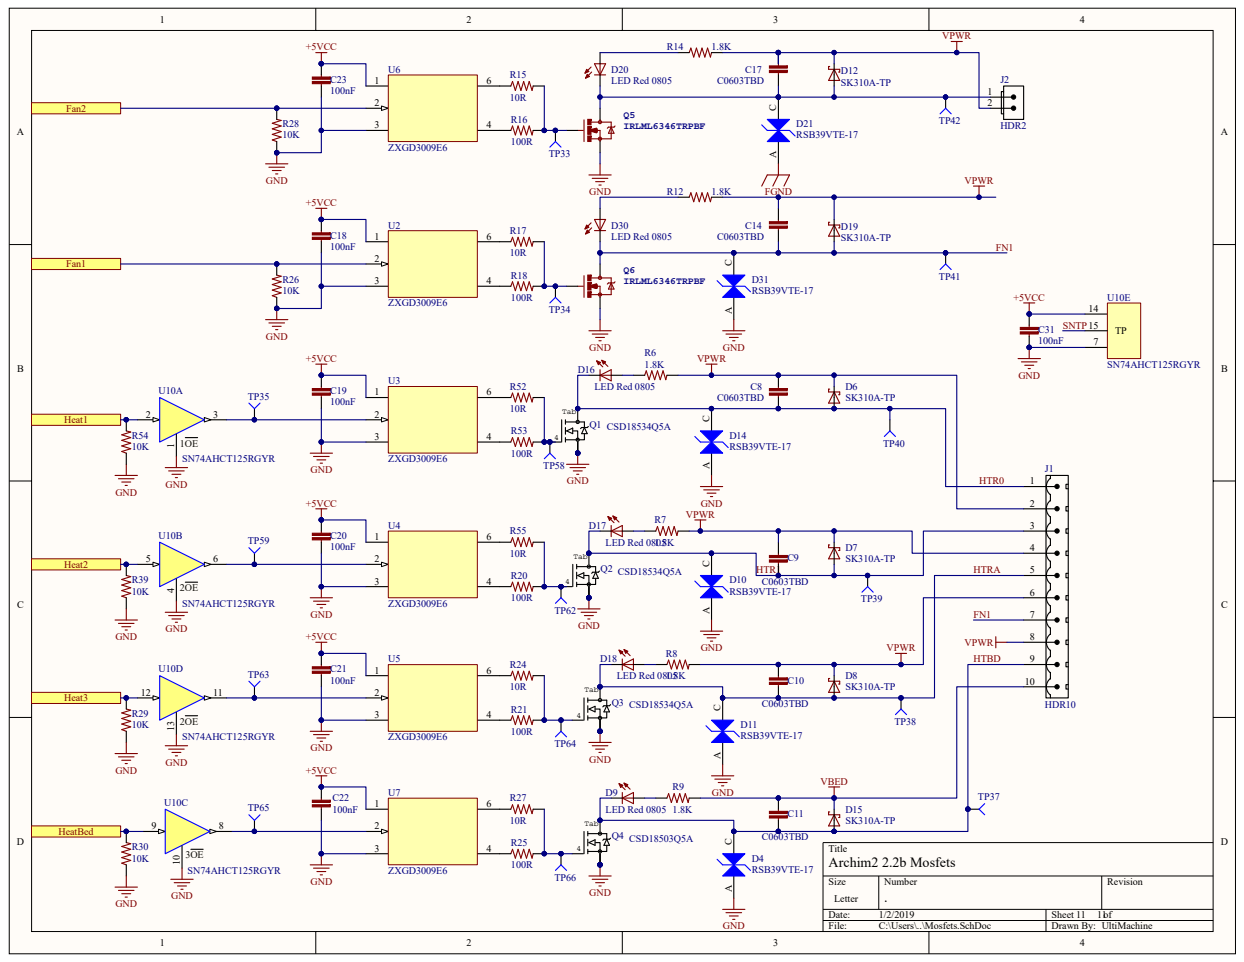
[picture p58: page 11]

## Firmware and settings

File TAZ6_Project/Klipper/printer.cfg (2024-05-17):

[include mainsail.cfg]
[include adxlmcu.cfg]
[include btt_sfs_v2_runout.cfg]
[include biqu_microprobe.cfg]
[include macros.cfg]

# host MCU service is preinstalled and ready to use with:
[mcu CB1]
serial: /tmp/klipper_host_mcu

[mcu]
serial: /dev/serial/by-id/usb-Klipper_sam3x8e_20312051505350373138303236303139-if00

[printer]
kinematics: cartesian
max_velocity: 300
max_accel: 1500
max_z_velocity: 7
max_z_accel: 100

#Settings configured by ADXL345 for Accelometer testing
[input_shaper]
shaper_type_x: ei
shaper_freq_x: 46.8
shaper_type_y: mzv
shaper_freq_y: 23.0

[stepper_x]
step_pin: PC6
dir_pin: PC5
enable_pin: !PC9
microsteps: 16
rotation_distance: 32
endstop_pin: ^PD4
position_endstop: -15
position_max: 300
position_min: -15
homing_speed: 75

[tmc2130 stepper_x]
cs_pin: PC7
run_current: .75
sense_resistor: 0.120
diag1_pin: !PA4
spi_software_sclk_pin: PD2
spi_software_mosi_pin: PD3
spi_software_miso_pin: PD1

[stepper_y]
step_pin: PC12
dir_pin: !PC11
enable_pin: !PC14
microsteps: 16
rotation_distance: 32
endstop_pin: PD6
position_endstop: -10
position_max: 303
position_min: -10
homing_speed: 75

[tmc2130 stepper_y]
cs_pin: PC13
run_current: .75
sense_resistor: 0.120
diag1_pin: !PC15
spi_software_sclk_pin: PD2
spi_software_mosi_pin: PD3
spi_software_miso_pin: PD1

[stepper_z]
step_pin: PC17
dir_pin: PC16
enable_pin: !PC19
microsteps: 16
rotation_distance: 2
endstop_pin: probe:z_virtual_endstop
#position_endstop: 0
position_max: 258
position_min: -3
homing_speed: 5

[tmc2130 stepper_z]
cs_pin: PC18
run_current: .90
sense_resistor: 0.120
diag1_pin: PC4
spi_software_sclk_pin: PD2
spi_software_mosi_pin: PD3
spi_software_miso_pin: PD1

[safe_z_home]
home_xy_position: 166,105 # Change coordinates to the center of your print bed
speed: 100
z_hop: 10                 # Move up 10mm
z_hop_speed: 100
#move_to_previous: True # errors out because it wants to move to a negative number

[extruder]
step_pin: PB10
dir_pin: !PC10
enable_pin: !PB22
microsteps: 16
rotation_distance: 7.81
nozzle_diameter: 0.400
filament_diameter: 1.75
heater_pin: PC24
sensor_type: ATC Semitec 104GT-2
sensor_pin: PB19
#control: pid  
#pid_Kp: 21
#pid_Ki: 1.78
#pid_Kd: 61.93
min_temp: 0
max_temp: 290
min_extrude_temp: 120
max_extrude_only_distance: 140.0
pressure_advance: .028

[tmc2130 extruder]
cs_pin: PC20
run_current: .75
sense_resistor: 0.120
diag1_pin: !PB23
spi_software_sclk_pin: PD2
spi_software_mosi_pin: PD3
spi_software_miso_pin: PD1

#[extruder1]
#step_pin: PB26
#dir_pin: PB24
#enable_pin: !PA11
#microsteps: 16
#rotation_distance: 33.500
#nozzle_diameter: 0.400
#filament_diameter: 1.750
#heater_pin: PC23
#sensor_type: ATC Semitec 104GT-2
#sensor_pin: PB18
#control: pid
#pid_Kp: 22.2
#pid_Ki: 1.08
#pid_Kd: 114
#min_temp: 0
#max_temp: 250

#[tmc2130 extruder1]
#cs_pin: PA10
#run_current: .5
#sense_resistor: 0.120
#diag1_pin: PD0
#spi_software_sclk_pin: PD2
#spi_software_mosi_pin: PD3
#spi_software_miso_pin: PD1

[heater_bed]
heater_pin: PC21
sensor_type: EPCOS 100K B57560G104F
sensor_pin: PB20
#control: pid
#pid_Kp: 21
#pid_Ki: 1.78
#pid_Kd: 61.93
min_temp: 0
max_temp: 120

[fan]
# print cooling fan
pin: PC23

#[heater_fan heatbreak_cooling_fan]
[heater_fan nozzle_cooling_fan]
# TAZ 6 internal case cooling fan - pin PC25
pin: PC25

[display]
lcd_type: st7920
cs_pin: EXP1_4
sclk_pin: EXP1_5
sid_pin: EXP1_3
encoder_pins: ^EXP2_3, ^EXP2_5
click_pin: ^!EXP1_2
#kill_pin: ^!EXP2_8

#[output_pin beeper]
#pin: EXP1_1

#cs_pin: PA29
#sclk_pin: PA27
#sid_pin: PC2
#encoder_pins: ^PJ6,^PJ5
#click_pin: ^!PE2
#menu_timeout: 5

########################################
# EXP1 / EXP2 (display) pins
########################################

[board_pins]
aliases:
    # EXP1 header
    EXP1_1=PA14, EXP1_3=PA15, EXP1_5=PA0,  EXP1_7=PA1, EXP1_9=<GND>,
    EXP1_2=PA13, EXP1_4=PA12, EXP1_6=PA16, EXP1_8=PC2, EXP1_10=<5V>,
    # EXP2 header
    EXP2_1=PA25, EXP2_3=PB27, EXP2_5=PA3,  EXP2_7=PB25,  EXP2_9=<GND>,
    EXP2_2=PA27, EXP2_4=PA29, EXP2_6=PA26, EXP2_8=<RST>, EXP2_10=<3.3V>
    # Pins EXP2_1, EXP2_6, EXP2_2 are also MISO, MOSI, SCK of bus "spi0"

# See the sample-lcd.cfg file for definitions of common LCD displays.

#Bed Mesh Configuration
[bed_mesh]
speed: 300
horizontal_move_z: 10  #How high to raise the Z between probe movements
mesh_min: 10, 45
mesh_max: 240, 290
probe_count: 15, 15  #Number of X and Y probe points in a grid
algorithm: bicubic
adaptive_margin: 5
#relative_reference_index: 12

#KlipperScreen Settings
[virtual_sdcard]
path: ~/printer_data/gcodes

[pause_resume]

[display_status]

#*# <---------------------- SAVE_CONFIG ---------------------->
#*# DO NOT EDIT THIS BLOCK OR BELOW. The contents are auto-generated.
#*#
#*# [probe]
#*# z_offset = 0.370
#*#
#*# [bed_mesh default]
#*# version = 1
#*# points =
#*# 	  -0.061250, -0.058750, -0.055938, -0.050313, -0.046875, -0.044375, -0.045313, -0.035625, -0.029375, -0.021250, -0.010625, 0.001250, 0.013750, 0.027500, 0.039375
#*# 	  -0.212188, -0.047500, -0.043750, -0.041875, -0.039063, -0.035000, -0.032188, -0.026875, -0.020938, -0.014375, -0.005000, 0.005937, 0.015937, 0.028437, 0.038125
#*# 	  -0.072813, -0.046563, -0.038438, -0.032500, -0.030625, -0.027813, -0.025000, -0.019375, -0.014063, -0.005625, 0.001562, 0.013125, 0.024062, 0.034687, 0.044687
#*# 	  -0.046250, -0.035000, -0.031250, -0.028750, -0.029063, -0.025938, -0.021875, -0.023125, -0.015313, -0.008750, -0.001563, 0.007187, 0.015000, 0.024375, 0.032187
#*# 	  -0.041875, -0.029375, -0.023125, -0.024063, -0.020313, -0.020938, -0.017188, -0.016875, -0.010938, -0.008125, -0.001250, 0.005937, 0.010937, 0.021562, 0.026875
#*# 	  -0.041250, -0.025625, -0.025313, -0.023438, -0.020938, -0.023750, -0.022188, -0.021250, -0.019063, -0.015000, -0.009375, -0.003750, 0.001250, 0.005000, 0.010625
#*# 	  -0.270000, -0.026563, -0.023750, -0.024688, -0.021875, -0.023750, -0.023750, -0.021875, -0.021563, -0.020625, -0.014688, -0.010000, -0.005313, -0.001875, 0.001875
#*# 	  -0.137813, -0.018750, -0.019063, -0.021875, -0.024375, -0.025938, -0.027188, -0.028125, -0.030938, -0.029063, -0.031250, -0.025000, -0.026875, -0.023125, -0.022813
#*# 	  -0.015313, -0.013125, -0.014688, -0.019063, -0.021250, -0.029063, -0.031250, -0.035938, -0.040000, -0.040313, -0.042188, -0.042500, -0.044375, -0.043750, -0.046563
#*# 	  -0.013438, -0.010938, -0.015625, -0.020625, -0.026875, -0.032188, -0.038438, -0.044688, -0.049063, -0.054375, -0.055313, -0.057500, -0.060313, -0.064063, -0.065938
#*# 	  -0.014375, -0.016250, -0.015938, -0.026250, -0.033750, -0.040313, -0.048438, -0.056563, -0.063125, -0.066250, -0.072500, -0.075313, -0.080000, -0.084375, -0.089375
#*# 	  -0.008750, -0.011875, -0.021563, -0.026875, -0.036875, -0.046875, -0.055000, -0.065625, -0.072188, -0.078750, -0.085000, -0.091250, -0.096250, -0.103125, -0.110938
#*# 	  -0.014063, -0.015625, -0.023125, -0.036563, -0.043750, -0.056250, -0.065000, -0.075313, -0.084063, -0.091563, -0.098438, -0.104688, -0.110313, -0.115938, -0.125000
#*# 	  -0.015313, -0.025625, -0.030938, -0.045625, -0.046250, -0.059688, -0.067500, -0.082500, -0.095000, -0.101250, -0.104375, -0.114688, -0.119688, -0.132188, -0.140313
#*# 	  -0.020625, -0.022813, -0.032813, -0.049063, -0.060000, -0.075313, -0.085938, -0.097813, -0.110313, -0.120000, -0.129063, -0.134063, -0.147813, -0.154688, -0.163125
#*# x_count = 15
#*# y_count = 15
#*# mesh_x_pps = 2
#*# mesh_y_pps = 2
#*# algo = bicubic
#*# tension = 0.2
#*# min_x = 10.0
#*# max_x = 239.88
#*# min_y = 45.0
#*# max_y = 290.0
#*#
#*# [extruder]
#*# control = pid
#*# pid_kp = 23.715
#*# pid_ki = 1.121
#*# pid_kd = 125.392
#*#
#*# [heater_bed]
#*# control = pid
#*# pid_kp = 61.460
#*# pid_ki = 1.418
#*# pid_kd = 666.068

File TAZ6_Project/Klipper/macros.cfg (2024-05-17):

# This file provides examples of Klipper G-Code macros.  The snippets
# in this file may be copied into the main printer.cfg file and
# customized.

# See docs/Config_Reference.md for a description of parameters.


######################################################################
# Start Print and End Print
######################################################################

# Replace the slicer's custom start and end g-code scripts with
# START_PRINT and END_PRINT. See docs/Slicers.md for more information on using these macros.

[gcode_macro PRINT_START]
gcode:
    M73 P0           # Clear progress bar
    M107             # Stop fans
    # Set printing status in LCD
    M117 Printing...
    # Use absolute coordinates
    G90
    # Get extruder and bed temperatures from slicer
    {% set BED_TEMP = params.BED_TEMP|default(60)|float %}
    {% set EXTRUDER_TEMP = params.EXTRUDER_TEMP|default(200)|float %}
    # Start bed heating
    M140 S{BED_TEMP}
    # Set and wait for nozzle to reach temperature
    M109 S{EXTRUDER_TEMP}
    # Wait for bed to reach temperature
    M190 S{BED_TEMP}
    # Home the printer
    G28
    BED_MESH_PROFILE LOAD=default
    
    # Create two lines to purge filament
    G1 X10 Y20 Z0.3 F5000.0        ; Move to start position
    G1 X10 Y200.0 Z0.3 F1500.0 E15 ; Draw the first line
    G1 X14 Y200.0 Z0.3 F5000.0     ; Move to side a little
    G1 X14 Y20 Z0.3 F1500.0 E30    ; Draw the second line
    G92 E0                         ; Reset Extruder
    G1 Z2.0 F3000 ; Move Z Axis up little to prevent scratching of Heat Bed


[gcode_macro PRINT_END]
gcode:
    # Wait for processes to end
    M400
    # Turn off bed, extruder, and fan
    M140 S0
    M104 S0
    TURN_OFF_HEATERS
    M107   # Turn off fan
    G91    # Relative positioning
    # Move nozzle away from print while retracting
    G1 X-2 Y-2 E-3 F300
    # Raise nozzle by 30mm
    G1 Z30 F3000
    G90    # Absolute positioning
    G1 Y280 F3000 # Move bed forward for part removal
    # Disable steppers
    # M84
    # Clear LCD Status
    M117
    # Beep for notification
    M300 P100

######################################################################
# Beeper
######################################################################

# M300 : Play tone. Beeper support, as commonly found on usual LCD
# displays (i.e. RepRapDiscount 2004 Smart Controller, RepRapDiscount
# 12864 Full Graphic). This defines a custom I/O pin and a custom
# GCODE macro.  Usage:
#   M300 [P<ms>] [S<Hz>]
#   P is the tone duration, S the tone frequency.
# The frequency won't be pitch perfect.

[pwm_cycle_time BEEPER_pin]
pin: EXP1_1
#   Beeper pin. This parameter must be provided.
#   ar37 is the default RAMPS/MKS pin.
value: 0
#   Silent at power on, set to 1 if active low.
shutdown_value: 0
#   Disable at emergency shutdown (no PWM would be available anyway).
cycle_time: 0.001
#   Default PWM frequency : 0.001 = 1ms will give a tone of 1kHz
#   Although not pitch perfect.

[gcode_macro M300]
gcode:
    # Use a default 1kHz tone if S is omitted.
    {% set S = params.S|default(1000)|int %}
    # Use a 10ms duration is P is omitted.
    {% set P = params.P|default(100)|int %}
    SET_PIN PIN=BEEPER_pin VALUE=0.5 CYCLE_TIME={ 1.0/S if S > 0 else 1 }
    G4 P{P}
    SET_PIN PIN=BEEPER_pin VALUE=0


######################################################################
# Filament Change
######################################################################

# M600: Filament Change. This macro will pause the printer, move the
# tool to the change position, and retract the filament 50mm. Adjust
# the retraction settings for your own extruder. After filament has
# been changed, the print can be resumed from its previous position
# with the "RESUME" gcode.

[pause_resume]

[gcode_macro M600]
gcode:
    {% set X = params.X|default(50)|float %}
    {% set Y = params.Y|default(0)|float %}
    {% set Z = params.Z|default(10)|float %}
    SAVE_GCODE_STATE NAME=M600_state
    PAUSE
    G91
    G1 E-.8 F2700
    G1 Z{Z}
    G90
    G1 X{X} Y{Y} F3000
    G91
    G1 E-50 F1000
    RESTORE_GCODE_STATE NAME=M600_state

######################################################################
# Override M117 command with rawparams
######################################################################

# The macro below will override the default M117 command to echo the message.
#
# It uses the rawparams pseudo-variable that contains the full unparsed
# parameters that was passed to the M117 command.
#
# As this can include comments, we are trimming the text when a `;` or `#` is
# found, and escaping any existing `"`

[gcode_macro M117]
rename_existing: M117.1
gcode:
  {% if rawparams %}
    {% set escaped_msg = rawparams.split(';', 1)[0].split('\x23', 1)[0]|replace('"', '\\"') %}
    SET_DISPLAY_TEXT MSG="{escaped_msg}"
    RESPOND TYPE=command MSG="{escaped_msg}"
  {% else %}
    SET_DISPLAY_TEXT
  {% endif %}

# SDCard 'looping' (aka Marlin M808 commands) support
#
# Support SDCard looping
[sdcard_loop]

# 'Marlin' style M808 compatibility macro for SDCard looping
[gcode_macro M808]
gcode:
    {% if params.K is not defined and params.L is defined %}SDCARD_LOOP_BEGIN COUNT={params.L|int}{% endif %}
    {% if params.K is not defined and params.L is not defined %}SDCARD_LOOP_END{% endif %}
    {% if params.K is defined and params.L is not defined %}SDCARD_LOOP_DESIST{% endif %}

# Cancel object (aka Marlin/RRF M486 commands) support
#
# Enable object exclusion - https://www.klipper3d.org/Exclude_Object.html
[exclude_object]

[gcode_macro M486]
gcode:
  # Parameters known to M486 are as follows:
  #   [C<flag>] Cancel the current object
  #   [P<index>] Cancel the object with the given index
  #   [S<index>] Set the index of the current object.
  #       If the object with the given index has been canceled, this will cause
  #       the firmware to skip to the next object. The value -1 is used to
  #       indicate something that isn’t an object and shouldn’t be skipped.
  #   [T<count>] Reset the state and set the number of objects
  #   [U<index>] Un-cancel the object with the given index. This command will be
  #       ignored if the object has already been skipped

  {% if 'exclude_object' not in printer %}
    {action_raise_error("[exclude_object] is not enabled")}
  {% endif %}

  {% if 'T' in params %}
    EXCLUDE_OBJECT RESET=1

    {% for i in range(params.T | int) %}
      EXCLUDE_OBJECT_DEFINE NAME={i}
    {% endfor %}
  {% endif %}

  {% if 'C' in params %}
    EXCLUDE_OBJECT CURRENT=1
  {% endif %}

  {% if 'P' in params %}
    EXCLUDE_OBJECT NAME={params.P}
  {% endif %}

  {% if 'S' in params %}
    {% if params.S == '-1' %}
      {% if printer.exclude_object.current_object %}
        EXCLUDE_OBJECT_END NAME={printer.exclude_object.current_object}
      {% endif %}
    {% else %}
      EXCLUDE_OBJECT_START NAME={params.S}
    {% endif %}
  {% endif %}

  {% if 'U' in params %}
    EXCLUDE_OBJECT RESET=1 NAME={params.U}
  {% endif %}


# Custom Load and Unload Filament macros
[gcode_macro LOAD_FILAMENT]
variable_load_distance:  50
variable_purge_distance:  10
gcode:
    {% set speed = params.SPEED|default(300) %}
    {% set max_velocity = printer.configfile.settings['extruder'].max_extrude_only_velocity  * 60 %}
    SAVE_GCODE_STATE NAME=load_state
    G91
    G92 E0
    G1 E{load_distance} F{max_velocity} # fast-load
    G1 E{purge_distance} F{speed} # purge
    RESTORE_GCODE_STATE NAME=load_state

[gcode_macro UNLOAD_FILAMENT]
variable_unload_distance:  50
variable_purge_distance:  10
gcode:
    {% set speed = params.SPEED|default(300) %}
    {% set max_velocity = printer.configfile.settings['extruder'].max_extrude_only_velocity  * 60 %}
    SAVE_GCODE_STATE NAME=unload_state
    G91
    G92 E0
    G1 E{purge_distance} F{speed} # purge
    G1 E-{unload_distance} F{max_velocity} # fast-unload
    RESTORE_GCODE_STATE NAME=unload_state

# Firmware filament retraction. This enables G10 (retract) and G11 (unretract) GCODE commands issued by many slicers. 
[firmware_retraction]
